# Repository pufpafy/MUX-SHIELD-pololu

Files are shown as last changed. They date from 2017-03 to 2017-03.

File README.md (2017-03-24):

# MUX-SHIELD-pololu
Платка щит за ардуино пололу A-Star 32U4 Mini SV 

Платката съдържа :

  2 драйвера (ULN2803 18 pin SOIC 1,27mm pitch) които са свързани към дигитални изходи на A-Star 32U4 Mini SV, а изходите на драйверите са свързани към хеадер в дясната част на платката. Целта е след хеадъра да управлява ел. вентили за пропускане на въздух под налягане.
http://bg.farnell.com/texas-instruments/uln2803adwr/darlington-transistor-array-full/dp/2437971

  1 аналогов мултиплексор-демултиплексор, (24 pin SSOP 0.65 mm pitch) изхода на който е свързан към аналогов вход A9 на A-Star 32U4 Mini SV, както и 4 управляващи пинчета, които са свързани към дигиталните крачета 
  13 Управляващ D;
  12 Управляващ C;
  11 Управляващ B;
  10 Управляващ А; 
  9 аналогов вход;
Целта на мултиплексора е да могат да се използват 16 аналогови входа за различни сензори
http://bg.farnell.com/texas-instruments/cd74hc4067sm96/ic-74hc-multiplexer-ssop24-full/dp/2435694

Допълнително са изкарани Хеадъри за MASTER_SLAVE Управление:
SDA-SCL header който се намира в наай-дплната лява част на платката.
RX-TX header , който се намира в най-долната дясна част на платката (преди headera за дигиталните изходи).

Както и хеадър за захранване.
5V-GND Header, който се намира най-горе в центъра на платката. Това е входното захранване, което трябва да е 5 волта постоянно напрежение

ЛЕВИЯ Хеадър (пиновете от ляво) са аналоговите входове, където първия вход е разположен най-ниско в платката, а 16 (последния) е разположен 2-ва пина преди най-горния. Tоест последния пин от долу-нагоре е VCC=5V, след това GND след това аналогов вход 16 (C15)

Десния хеадър (пиновете от дясно) са дигитални изходи, служещи за управление на вентили за пропускане на въздух. Пина разположен най- долу е Вентил 1 , а пина разположен 2 пина преди последния е Вентил 16 (отново на последно място е разположено захранването VCC=5, а преди него GND) (след време тук може да се опише кой вентил за коя става отговаря)

!!!Внимание !! в десния хеадър посредата има 2 (9 и 10) неактивни пина, които не се използват за нищо 

Резистора R1 служи за подаване на логическа '0' на пина EN на мултиплексора, с което той се активира. (най-долу в центъра) 
Поставена е възможност за светодиодна индикация, коята да свети при включване на захранването към платката. Намираща се най-горе в ляво. 
Резистора R2 служи, като предпазителен резистор за светодиода
Поставена е възможност за разделителен кондензатор C1 , между VCC=GND (най- горе в дясно )

След проектирането са открити следните нередности :
-солдер маската, която индикира буквено и цифрово номерата на крачетата е прекалено малка за да се чете.
-дясната страна на платката е прекалено дебела, което не позволява да се прикрепят стандартни хеадери, следва да се стесни чрез изпилване.
-масате от дясната страна на платката, на вътрешния хеадър не е свързана с останалите маси. Тази маса е свързана единствено към втори драйве (D2). Следователно за да протече ток през този драйвер, тока трябва да премине през платката пололу. След оглед на платката пололу е установено че пистата е достатъчно голяма да допусне нужния ток.
-Знакът за маса при захранващия хеадър е със кръгла форма а не с квадратна
-платка 0 е пробна платка, която има късо на мултиплексора (тренировъчна за запояване на смд 0,65)

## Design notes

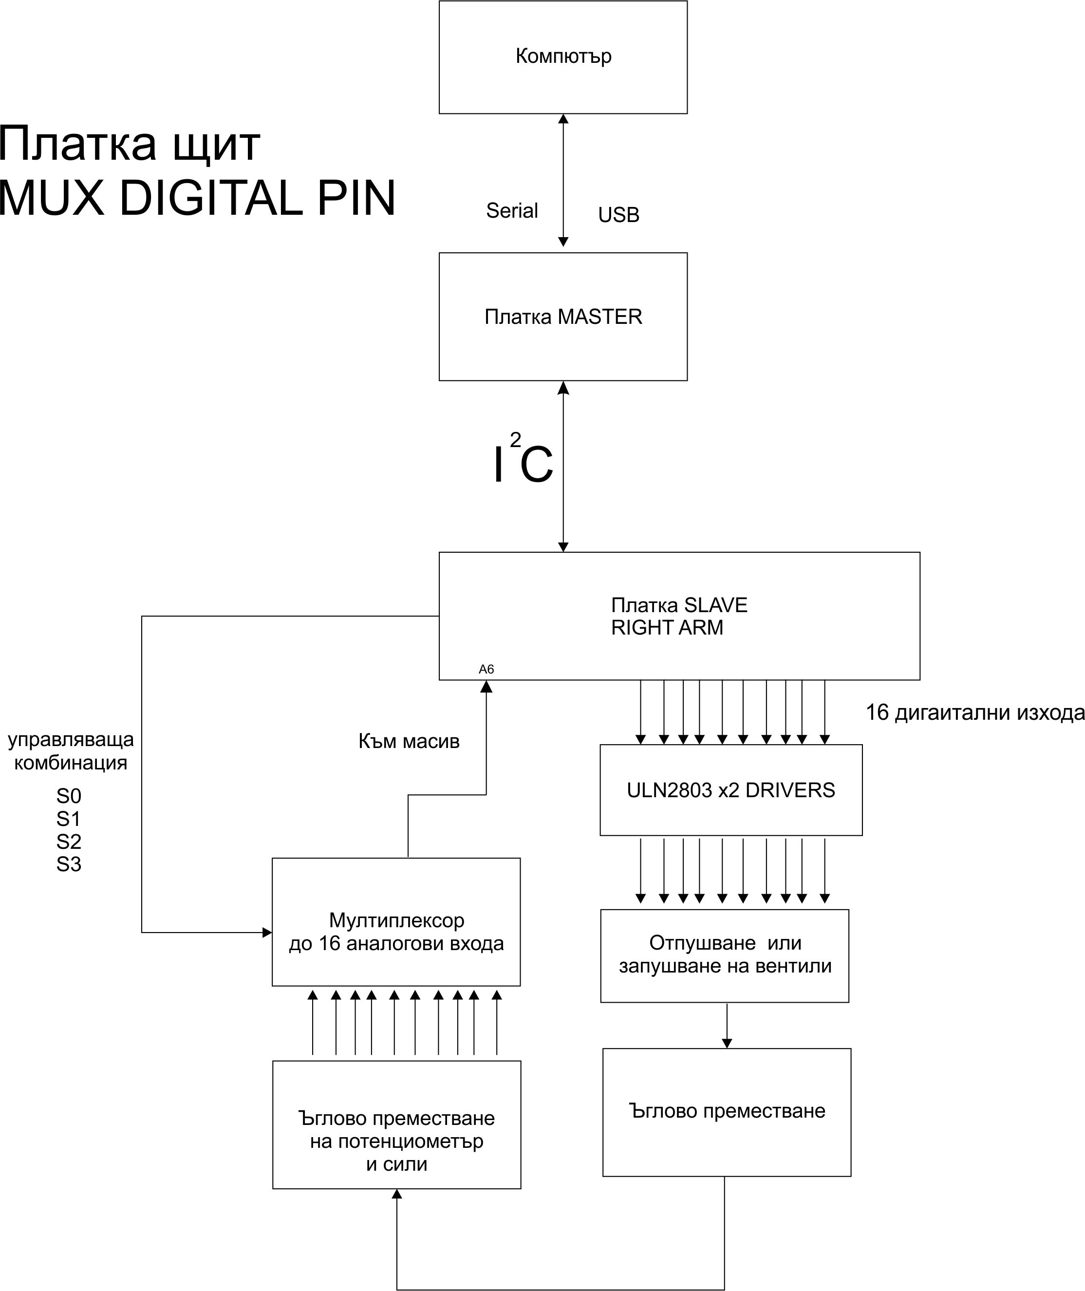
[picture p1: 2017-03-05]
схема ардуино мастър слейв analog input MUX digital pin outut.jpg

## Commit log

2017-03-05 mux digital pin schematic added
    altium designer schematic for pololu Shield mux digital pin 28.02.2017
    [schematic MUX_DEMUX.SchDoc]
2017-03-05 PCB added
    altium designer PCB schematic for A-Star 32U4 Mini SV SHIELD mux Digital pin 28.02.2017
    [MUX DIGITAL PIN PCB.PcbDoc]
2017-03-05 Начално въвеждане на READ-ME
    полълване на READ-me , обяснение за главните елементи на платката
2017-03-05 Pin map table added
    добавяне таблица на ексел, която показва начина на свързване межу SHIELD и POLOLU a-star
    [PIN MAP MUX SHIELD DIGITAL PIN.xlsx]
2017-03-05 Block diagram added
    добавяне на блок схема, описваща начина на работа
2017-03-05 Arduino pololu PCB FOOTPRIN
    Altium designer PCB-footprint за A-Star 32U4 Mini SV
    [arduino pololu holes fixed.PcbLib]
2017-03-05 MUX PCB footprint SSOP 0,65
    altium designer MUX PCB footprint SSOP 0,65
    ако не се вижда първоначално да се натисне tools->next component
    [MUX FIXED PCB FOOTPRINT.PcbLib]
2017-03-05 Driver PCB FOOTPRINT added
    ULN2803 18 pin SOIC 1,27mm pitch
    [uln2803Soic.PcbLib]
2017-03-05 schematic library
    ардуино пололу
    мултиплексор
    драйвер
    драйвер огледален
    [Arduino pololu.SchLib, CD74HC4067.SchLib, ULN2803A SOIC mirrored.SchLib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]
2017-03-05 Project file added
    Mux digital pin project file,
    името е сгрешено
    [MUX_DEMUX_Project.PrjPCB]
2017-03-24 първи поглед след печатане
